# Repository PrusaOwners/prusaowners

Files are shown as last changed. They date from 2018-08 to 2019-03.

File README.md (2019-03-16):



# PrusaOwners

This is a wiki for the Original Prusa printers created by Josef Prusa and any projects related to these printers.

## Printer Information

### Prusa i3 Official Links
- [MK3 Features](https://www.prusa3d.com/original-prusa-i3-mk3/)
- [MK2s Features](https://www.prusa3d.com/prusa-i3-kit)
- [Printing Handbook](https://www.prusa3d.com/downloads/manual/prusa3d_manual_175_en.pdf)
- [Manuals and Guides](https://manual.prusa3d.com/c/English_manuals)
- [Drivers and downloads](https://www.prusa3d.com/drivers/)
- [Maintenance Guides](https://help.prusa3d.com/l/en/category/A6PvLnaCoU-maintenance)
- [Knowledge Base](https://help.prusa3d.com/l/en)
- [Store](https://shop.prusa3d.com/en/)

### Communities
- [Prusaowners Discord Server (The 602 Wasteland)](https://discord.gg/hYUjSnW)
- [Official Prusa Forums](https://shop.prusa3d.com/forum)
- [Original Josef Prusa i3/MK2/S/3 Owners](https://www.facebook.com/groups/Prusai3users/)
- [Prusa Community Forum and Custom Mods](https://www.facebook.com/groups/prusacommunity/)
- [Prusa I3 MK2/S/3 - FR (french)](https://www.facebook.com/groups/prusai3mk2s/)
- [Haribo 3030 Upgrade](https://github.com/PrusaMK2Users/3030_Haribo_Edition/)
- [Prusa i3 Bear Upgrade](https://www.facebook.com/groups/prusabearupgrade/)
- [3d Printing Matttermost Server](https://3dprinting.community)
- [r/prusa3d subreddit](https://www.reddit.com/r/prusa3d/)
- [r/prusa3d Discord](https://discord.gg/z7wMpfn)

## Resources

### Printer Specifications and Parts
- [MK3 Compatible Parts](MK3_Compatible_Parts.md)
- [EinsyRambo Specifications](https://reprap.org/wiki/EinsyRambo)
- [TMC2130 Stepper Driver Datasheet](https://www.trinamic.com/fileadmin/assets/Products/ICs_Documents/TMC2130_datasheet.pdf)

### Firmware
- [Klipper](Klipper.md)
- [Klipper MK3 Firmware G-Code Reference](https://github.com/KevinOConnor/klipper/blob/master/docs/G-Codes.md)
- [Prusa Official Firmware](https://github.com/prusa3d/Prusa-Firmware)
- [Prusa Official MK3 Firmware G-Code Reference](https://github.com/prusa3d/Prusa-Firmware/blob/MK3/Firmware/Marlin_main.cpp#L152)

### Slicing Software
- [Slicer Profiles](Slicer_Profiles.md)
- [Test Prints](Test_Prints.md)

### PrusaOwners Repositories
- [Main Github](https://github.com/PrusaOwners/prusaowners/)

### Community To Do List
- [Community To Do List for i3 MK3](Community_To_Do_List_for_i3_MK3.md)

## How To Guides

### How To Guides
- [Cold Pull on MK3](Cold_Pull_on_MK3.md)
- [gregsaun's maker cheatsheet](https://github.com/gregsaun/maker_cheatsheet)
- [Manual print based PINDA temperature calibration](Manual_print_based_PINDA_temperature_calibration.md)
- [First layer and PINDA temperature calibration with calipers](First_layer_and_PINDA_temperature_calibration_with_calipers.md)

### Mods and Improvements
- [Bed Leveling with Wave Springs](Bed_Leveling_with_Wave_Springs.md)
- [Bed Leveling without Wave Springs](Bed_Leveling_without_Wave_Springs.md)
- [Improved Rigid Feet](https://www.thingiverse.com/thing:2802540)
- [Improved Z-axis mounts by jltx](Improved_Z-axis_mounts_by_jltx.md)
- [Metal MK3 parts](Metal_Mk3_parts.md)
- [S3l3ctor](S3l3ctor.md)
- [Reverse Bowden](https://www.thingiverse.com/thing:2783385)
- [Skelestruder by jltx](Skelestruder_by_jltx.md)
- [How to make prints better on the mk3](How_to_make_prints_better_on_the_mk3.md)
- [PLA bearings](PLA_bearings.md)
- [Einsy fan voltage mod](Einsy_fan_voltage_mod.md)
- [Moons stepper motors](Moons_stepper_motors.md)
- [MK2 PINDA temp retrofit](https://github.com/PrusaOwners/prusaowners/blob/master/MK2%20PINDA%20temperature%20compensation%20retrofit.md)
- [Bear upgrade frame](https://github.com/gregsaun/prusa_i3_bear_upgrade)
- [Bear upgrade extruder and X axis](https://github.com/gregsaun/bear_extruder_and_x_axis)

### Octoprint
- [Prusa Guide: Octoprint for i3 MK3 using Pi Zero W to Einsy Headers](https://manual.prusa3d.com/c/Octoprint_for_Original_Prusa_i3_MK3)
- [PrusaMeshMap Plugin for Octoprint](https://github.com/PrusaOwners/OctoPrint-PrusaMeshMap)

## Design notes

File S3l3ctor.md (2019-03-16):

[This is S3l3ctor](https://github.com/PrusaOwners/s3l3ctor/blob/master/images/s3l3ctor.png), an open source, sub $100, 6 chroma filament selector system currently under development. You can print any color (up to 6) you want without changing your extruder design.

S3l3ctor is:
* A 100% open source filament selector
* Costs under $120
* Can use up to 6 colors at once
* Lets you keep your extruder
* Can work on any printer with a USB port or spare pins
* Being developed by Matt when he's not doing homework
* Is undergoing closed Alpha testing right now

S3l3ctor is **not**:
* Done yet
* Accepting donations not made in 4043d
* A MMU2 clone
* Requires changing extruder hardware
* For the faint of heart (yet!)

S3l3ctor is an open source filament selector under development. Development is being led by ThatMattGuy (Matt) in collaboration with other community members.

At this point the project is undergoing closed alpha testing and will have an open beta starting soon<sup>TM</sup>. I mean you print the parts, but it's likely not a good idea yet.

[Link the the Github STLs](https://github.com/PrusaOwners/s3l3ctor).

# BOM

## Printed Parts:

| STL Name | Quantity |
| ---- | ---- |
| MainBodyV2 | 1 |
| barrelidlerholder_v2.STL | 1 |
| barrelMotorholder_v2 .STL | 1|
| A1R1__Body_spring_x2.STL | 0|
| A1R1_AssemblyHolder_x2.STL | 2 |
| RetainerV2.STL | 2 |
| A1R1_SplitterShroom_x1.stl | 1 |
| A1R1_tumblerV64_maleEnd_x1.stl | 1 |
| A1R1_tumblerV64_motorEnd_x1.stl | 1 |
| A1R1_tumblerV69_pin_x6.stl | 6 |
| A1R1_tumblerV69_withsupports__x6.stl | 6 |
| For Skelestruder People: | |
| PC4-m10_SKELESTRUDER_B1.stl | 1|

## Hardware:

| Item | Quantity | Example link | 
|---- | ---- | ----|
| Bolts | (how many? What size?) | Soon^tm |
| Square nuts | 2 | Spares bag| 
| 608 bearings | 8 | [ebay](<https://www.ebay.com/itm/8pcs-625-2Z-625-ZZ-C3-Double-Metal-Shielded-Ball-Bearing-5x16x-5mm-US-Stock-M496/401542781331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>)  |
|Mk8 Gears| 6 | [Amazon](<https://www.amazon.com/BALITENSEN-Direct-Extruder-Reprap-Effective/dp/B07792SHML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>) |
|Pc4-M10 fittings, pass through or drill them out | 7| soon^tm|
|PTFE tubing ID 2mm OD 4mm | couple meters | [ebay](<https://www.ebay.com/itm/PTFE-Bowden-Teflon-Tube-1-75-Filament-3D-printer-RepRap-Rostock-Kossel/162932641530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>) |

## Electronics:

| Item | Quantity | Notes and URL|
|----|----|----|
|RAMPS + 5x A4988 drivers + Mega kit | 1 | [ebay link](https://www.ebay.com/itm/3D-Printer-Kit-RAMPS-1-4-Mega2560-A4988-12864-LCD-Controller-for-Arduino-Reprap-/252181241032) - TODO find a better kit link |
|**POWER OPTIONS**|||
|12v 2 amp power brick| 1| If you want to externally power S3l3ctor - [Example brick](https://www.amazon.com/Amamax%C2%AE-Wall-Adapter-Power-Supply/dp/B00KZ2ZQE8) - TODO find a better example
|12v 2 amp buck converter| 1| OPTIONAL - For those who want to run off a 24v PSU. Make sure you have enough PSU headroom! [Example](https://www.amazon.com/Converter-Step-Down-Module-Voltage-DCCON-CPT245/dp/B00BNPYBM4) - TODO verify links
| If you have a 12v PSU and want to power off the PSU| |You're fine, nothing needed here :D |
||||
| Microswitch with bearings | 9| [Something like this](https://www.google.com/url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)

For a RAMPS setup: Set of RAMPS plus at least 2x A4988s (usually 5x) plus Mega Either a 12v brick (2 or more amps) or 24v to 12v buck regulator off of printer PSU 2x NEMA 17s 7-8x microswitches with bearings

# Assembly

## Tumbler

### Shaft preperation

Begin by filing, grinding or otherwise abrating a flat a mm or two deep (doesn't really matter), and about 5mm long. While you have the shaft out, make sure that your 625 bearings will slide smoothly along the shaft. They shouldn't slide smoothly like a linear bearing, but at the same time they should not need pounding. A more scientific way to quantify this is with a calipers - if the bearings' ID is more than 30 micron undersized (4.97mm or so), the fit on the 5mm rod is going to be close. Like, probubly too close. I reccomend measuring bearings and 

## Main Body

## Magic Mushroom

## Electronics

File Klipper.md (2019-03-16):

About Klipper
-------------

Klipper is a 3D printer firmware system which utilizes an external processor such as a Raspberry Pi or other computer to compute kinematic equations and send the processed information to the MCU on the printer, usually a ATMega 2560. Klipper's main fork is available at <https://github.com/KevinOConnor/klipper>, however, if you want the experimental features outlined in this wiki it is recommended to clone our community repository at <https://github.com/PrusaOwners/klipper>.

Installing and Configuring Klipper on the MK3
---------------------------------------------

If you are installing Klipper on a Raspberry Pi, follow the instructions [Adafruit's put together here](https://learn.adafruit.com/octoprint-on-m3d/octoprint-set-up) to install Octoprint, or use a preconfigured octopi image.

First, SSH into the Pi (Windows: use PuTTY; Linux/Mac, use the terminal). If you don’t know what it is, try octopi.local or install something like Advanced IP Scanner to find it out. Username is pi, password raspberry

Run the following commands:

    git clone https://github.com/PrusaOwners/klipper
    ./klipper/scripts/install-octopi.sh
    cd ~/klipper/
    make menuconfig

Leave everything as stock, and click save, then exit.

Run the following command:

    make

Ensure that the Raspberry Pi is physically connected to the printer, and that Octoprint is not connected to the printer by navigating to <http://octopi.local> or your pi’s IP address on a web browser (the "Connect" button should be displayed).

Next is finding the USB serial port.  The general way to find a USB serial port is to run ls -l /dev/serial/by-id/ from an ssh terminal on the host machine. It will likely produce output similar to the following:

    lrwxrwxrwx 1 root root 13 Jun  1 21:12 usb-1a86_USB2.0-Serial-if00-port0 -> ../../ttyUSB0
The name found in the above command (minus the -> ../../ttyACM0 portion) is stable and it should be used in the config file and while flashing the micro-controller code. For example, a flash command might look similar to:

    sudo service klipper stop
    make flash FLASH_DEVICE=/dev/serial/by-id/usb-1a86_USB2.0-Serial-if00-port0
    sudo service klipper start

Next, copy the file ~/klipper/config/printer-prusa-i3-mk3-2017.cfg to your home directory and rename it printer.cfg:

    cd ~
    cp ~/klipper/config/printer-prusa-i3-mk3-2017.cfg printer.cfg

This file contains a default configuration for the Prusa i3 MK3 and enables all of the experimental features outlined in this wiki.  The config must be updated with the updated USB information.  Open up printer.cfg in a text editor and change the line listed below:

    [mcu]
    serial: /dev/ttyACM0

to match the the USB device from the ls -l command.  Be sure to copy-and-paste the name from the "ls" command (minus the -> ../../ttyACM0 portion) that you ran above as the name will be different for each printer.  The line in the updated config might look like:

    [mcu]
    serial: /dev/serial/by-id/usb-1a86_USB2.0-Serial-if00-port0

Next, restart Klipper with the following command:

    sudo service klipper restart

Finally, connect Klipper to Octoprint:

Go to the setting wrench at the top.

Under **“Serial Connection”** in **“Additional serial ports”** add **“/tmp/printer”**. Then click **“Save”**.

Enter the Settings tab again and under **“Serial Connection”** change the **“Serial Port”** setting to **“/tmp/printer”**. Navigate to the **“Behavior”** sub-tab and select the **“Cancel any ongoing prints but stay connected to the printer”** option. Click **“Save”**.

From the main page, under the **“Connection”** section (at the top left of the page) make sure the **“Serial Port”** is set to **“/tmp/printer”** and baudrate is **250000** and click **“Connect”**. (If **“/tmp/printer”** is not an available selection then try reloading the page.)

Once connected, navigate to the **“Terminal”** tab and type **“status”** (without the quotes) into the command entry box and click **“Send”**. If you see this, you’re good: **“Recv: // Printer is ready”**

Special considerations for installing on a non-raspberry-pi
-----------------------------------------------------------

If you follow the above instructions and it doesn't work, try running this:

cat /etc/default/klipper

You should get an output like this:

    # Configuration for /etc/init.d/klipper

    KLIPPY_USER=server

    KLIPPY_EXEC=/home/server/klippy-env/bin/python

    KLIPPY_ARGS="/home/server/OctoPrint/klipper/klippy/klippy.py /home/server/printer.cfg -l /tmp/klippy.log"

If KLIPPY_ARGS's path is different than your klipper path (e.g. this example shows Klipper under the Octoprint folder, and I had it in /home/server), correct with a mv command like so: mv /home/YourUserName/klipper /home/YourUserName/OctoPrint/klipper

Calibrating your Z-Endstop
--------------------------

The Prusa i3 MK3 uses the Pinda probe as a Z-Endstop, and the endstop height needs to be calibrated prior to printing. Proceed with the following steps for initial calibration:

1.  Set the following properties under [stepper_z] in your printer.cfg:

        position_min: -2
    and under [probe]:

        z_offset: 0

2.  Restart klipper from the shell to load the new config:

        sudo service klipper restart

    Alternatively, you can issue a restart command from Octoprint's terminal if you are connected.

3.  Home the Z-axis using Octoprint.
4.  Use Octoprint or the Printer Menu to move the Z-axis down in .1mm to .01mm increments until the nozzle is just above the bed
5.  The current Z position will likely be somewhere between -0.4 and -1.0 It will be displayed on the printer, you can also retrieve the current position by issuing the GET_POSITION command in Octoprint's terminal.
6.  The absolute value of the current Z position will be your endstop position and probe offset. For example, if your Z position is -.6, enter the following under [probe]:

        z_offset: .6

7.  Restart Klipper again and you are ready to print. You may have to make slight changes to get a good first layer. Increasing the endstop position will bring the nozzle closer to the bed when printing, decreasing the endstop will raise it. Make sure you update both the endstop position and probe offset when making changes.

Prusa GCode Support
--------------------

Currently the following prusa specific gcodes are supported:

-   TIMED_GCODE
-   TRAM_Z

To enable these gcodes, add the following to your printer.cfg:

    [prusa_gcodes]

TIMED_GCODE allows the user to execute a gcode with a specific delay.  This is, for example, useful for resetting the display after a M117 message.  It is used in the following manner:

    TIMED_GCODE GCODE=M117 DELAY=5

The example above will send an empty M117 with a delay of 5 seconds.  Note that if you want to execute a more complex gcode, spaces should be replaced underscores.  For example, if you want to send M117 Hello on a with a delay of 10 seconds, you could enter the following:

     TIMED_GCODE GCODE=M117_Hello DELAY=5

TRAM_Z functions in a manner similar to Prusa's Calibrate-Z functionality. It will use the TMC2130 driver to home to the top of the printer, then move an extra 10mm to “tram” the Z-Axis.

Note for previous users:
LOAD_FILAMENT, UNLOAD_FILAMENT, SET_BEEPER, and M900 have been deprecated.  It is recommend to use gcode macros to replace the functionality of these gcodes.

Configuring Mesh Bed Leveling
-----------------------------

### About Klipper Mesh Bed Leveling

Mesh Bed Leveling is now available in upstream Klipper: <https://github.com/KevinOConnor/klipper>

You may also pull it from the PrusaOwners repo: <https://github.com/PrusaOwners/klipper/>

### Things to Note Before Implementing

There are a few things to keep in mind with this implementation that may be subject to change:

1.  By default each probe point is only sampled once, unlike Prusa Firmware which samples twice. After testing this doesn't seem to create an issue, as the Pinda produces fairly repeatable results. Functionality has been added to multi-sample points, with the tradeoff being that there is a small pause between samples unlike stock firmware.
2.  <b>Those transitioning from ALPHA versions of bed_mesh should be aware of the following:</b>
    1.  The probe_offset option of [bed_mesh] has now moved to the [probe] section as x_offset and y_offset.
    2.  In the [bed_mesh] section probe_min and probe_max have been renamed to min_point and max_point.
    3.  G80 and G81 aliases are no longer hardcoded. Instructions for how to add aliases via gcode_macros are provided later in this document.
    4.  After probing the tool no longer returns to (0,0), as this is not suitable for every printer. This can be added in a gcode_macro or in your slicer's start gcode.

### Pre-requisites

Before proceeding, make sure [bed_tilt] is not in your printer.cfg. It will present a conflict with Mesh Leveling. You also need [probe] in your printer.cfg:

    [probe]
    pin: PB4
    x_offset: 24.
    y_offset: 5.
    z_offset: .0
    speed: 10.0

The z_offset is the distance between the nozzle and the print surface when the probe triggers.  When a probe is used as an endstop for the z axis, the value for z_offset will be used as the endstop position.  Thus, if you have position_endstop in [stepper_z] defined, remove it.  The x_offset and y_offset options refer to the distance between the nozzle and the probe on their respective axis.

It is also a good idea to make sure position_min under [stepper_z] is a negative number. Its likely that you will need to move below Z0 if your bed is significantly warped.

Finally, I recommend adding a homing override to to home to the center of the bed:

    [homing_override]
    gcode:
     G1 Z3
     G28 X0 Y0
     G1 X101 Y100 F5000
     G28 Z0
    set_position_z: 0

This will lift Z 3mm prior to homing, making sure that it doesn't crash into the bed if its location is close to the build plate. It will then home X and Y, move X and Y so that the probe is at the center of the build plate, then home Z.

### Configuration

Mesh Leveling is fully parametric. As a result it is possible to configure it for any printer, and a varying number of probe points. Probe points are generated dynamically. To get started with Mesh Leveling, the bare minimum is required in printer.cfg:

    [bed_mesh]
    speed: 100
    min_point: 11,1
    max_point: 215,193

Below is what a Mesh Bed Leveling configuration would look like with all options set:

    [bed_mesh]
    speed: 100
    horizontal_move_z: 5
    samples: 1
    sample_retract_dist: 2.0
    min_point: 11,1
    max_point: 215,193
    probe_count: 3,3
    fade_start: 1.0
    fade_end: 10.0
    move_check_distance: 5.0
    split_delta_z: .025
    mesh_pps: 2,2
    algorithm: lagrange
    bicubic_tension: .2

Be aware that when dynamically generating points the distance between each point is calculated. If the distance is not a whole number, the value will be floored to the last hundredth. This will result in your maximum points being adjusted inward slightly. Also keep in mind that the min and max points refer to the position of the nozzle, not the probe. Make sure you do not choose points that will move the probe off of the bed.

Below is a detailed explanation of each option:

-   speed:

The speed at which the bed is probed.

-   horizontal_move_z:

The distance to raise the toolhead between probes. Default is 5mm.

-   samples:

The number of samples to take for each probe point.

-   sample_retract_dist:

The distance to retract the tool between samples.  Only applies when samples > 1.

-   min_point:

The minimum start point (x,y) on the grid to generate. This parameter must be provided.

-   max_point:

The maximum start point (x,y) on the grid to generate. Note that this may not be the 'last' point if probing an even number of Y values on the grid. This parameter must be provided.

-   probe_count:

A comma separated pair of integers (x,y) indicating the number of points to probe on each axis. It is possible to enter a single integer value for this parameter, in which case it will be applied to both axes. Default is 3,3.

-   fade_start:

The z position in which to start fading out z_adjustment. Default is 1.0

-   fade_end:

The z position in which fading will complete. If fade_end is less than or equal to fade_start then fading will be disabled. Be careful with this setting, fading too quickly will likely result in a failed print, or could potentially crash the nozzle into the bed if done near Z0. Default is 10.0

-   move_check_distance:

The minimum distance a move can be split. Default is 5.0

-   split_delta_z:

The minimum amount of z-difference that will trigger a split move. The check algorithm will traverse a move by the amount specified in move_check_distance until it finds a z-delta greater than or equal to split_delta_z. Default is 0.025

-   mesh_pps:

A comma separated pair of integers (x,y) indicating the number of points to interpolate for each segment in the axis. Consider a 3x3 probed grid. There are two “segments” between the X points, and two between the Y points. If you specify mesh_pps: 3,3 then there will be 6 interpolated points and 3 probe points in the mesh along each axis, for a total of 81 points in the mesh. If this is set to zero, then no interpolation will be done on the axis. Note that this value can also be a single integer, in which case the number is applied to both axes. Default is 2,2.

-   algorithm:

The interpolation algorithm to use. May be either “lagrange” or “bicubic”. 3x3, 4x3, and 3x4 meshes must use lagrange, 4x4 or above may choose either. Default is lagrange.

-   bicubic_tension:

The bicubic interpolation algorithm uses cardinal hermite spline interpolation. A “tension” parameter may be entered to influence the amount of slope interpolated in the curve. That is, a higher tension will will make the mesh more curvy, and zero tension will be closer to bilinear interpolation. Be careful with this setting as generating steep hills and valleys in the mesh may cause the the nozzle to crash. This setting will be ignored if not using bicubic interpolation. Default is 0.2.

### Bed Mesh Gcodes

    BED_MESH_CALIBRATE

Initiates the calibration procedure (ie probes the bed and builds the mesh).

    BED_MESH_OUTPUT

Prints the results of the Mesh to the terminal.

    BED_MESH_MAP

This will probe the bed, serialize the points, and send them to the terminal. No mesh will be generated during this procedure, so no correction will be applied. It will however clear any prior mesh data. The purpose of this gcode is to allow for Octoprint plugins such as PrusaMeshMap to easily fetch probe data from a large number of sampled points. This has not yet been implemented in any plugins, but the functionality is there for those who wish to take advantage of it.

    BED_MESH_CLEAR

This will clear the mesh from memory. No further Z adjustment will be performed after a clear.

    BED_MESH_PROFILE LOAD=<name> SAVE=<name> REMOVE=<name>

BED_MESH_PROFILE can be used to save mesh state to persistent storage.  This isn't advised for MK3 users as bed geometry may not be consistent between prints, However users with rigid beds and glass surfaces may find this functionality useful.

### Generating Aliases

To generate gcode aliases, the following can be added to your printer.cfg:

    [gcode_macro G80]
    gcode:
     G28
     BED_MESH_CALIBRATE
     G1 X0 Y0 Z0.4 F4000

    [gcode_macro G81]
    gcode:
     BED_MESH_OUTPUT

This will create G80 and G81 aliases respectively. Also, as you can see, the G80 Macro moves the tool back to the origin after calibration. You can alter this GCode line to move it where you please at a speed that best suits your printer.

### Final Notes

-   Generally probing a 3x3 grid with default mesh values will produce the desired result. However, one may wish to experiment with more probe points and different interpolation algorithms to eliminate deadspots. Lagrange interpolation tends to oscillate as the number of samples increase, so it is recommended to use bicubic interpolation for larger probe grids.

Bed Skew Correction:
--------------------
TODO (COMING SOON)

Pressure Advance
----------------

The next thing you'll have to do is to configure _Pressure Advance_ (from this point downwards _PA_). Without _PA_ you will be getting ugly prints with blobs and curling at corners and lots of oozing. There is a [guide](https://github.com/KevinOConnor/klipper/blob/master/docs/Pressure_Advance.md) on how to configure _PA_ in the main Klipper repository, but it is complex and requires lots of manual steps. Read it through to understand what it is about, but don't actually follow it. We provide a setup process which is mode advanced and simpler at the same time, where you only have to print one test object from which you can derive the _PA_ value. The guide is [here](Pressure_Advance.md).

[Alpha] Probe Temperature Compensation
----------------------------------------

Initial support has been added for probe temperature drift compensation. In its current form temperature compensation is configured manually, in a similar fashion to the method used in stock Prusa firmware.

To enabled Probe temperature support, add the following to your printer.cfg:

    [probe_temp]
    sensor_type: EPCOS 100K B57560G104F
    sensor_pin: PF3
    t_offsets:
     35.0, 0.0
     40.0, 0.02
     45.0, 0.06
     50.0, 0.120
     55.0, 0.2
     60.0, 0.3

Note that the offsets above are Prusa Firmware's defaults. Also note the space padding the front of each offset. This is <b>required</b>, otherwise Klipper's parser will get confused.

The following gcodes are added with this module:

    GET_PROBE_TEMP

This simply returns the probe's current temperature to octoprints terminal

    PROBE_WAIT TEMP=<Target Temperature> TIMEOUT=<SECONDS>

Use the gcode above to wait for the probe to reach a certain temperature. The minimum target is 20, maximum is 70. The direction is automatically determined by the heater state.  If both heaters are off then the gcode will wait for the probe to cool to the supplied temperture, otherwise it will wait for it to heat.  Timeout sets a timeout in minutes. If the timeout is reached the printer will stop waiting and no changes will be made to the offset. A timeout value of 0 will wait indefinitely, which is the default value. 

    APPLY_TEMP_OFFSET

The gcode above will look up the probe's current temperatue, calculate the offset to apply based on the supplied parameters, then adjust the gcode offset by that amount.

### Manual Calibration Procedure

1.  Before Calibrating, make sure to remove t_offsets and all of its associated values from printer.cfg, then restart Klipper. This will make sure that no additional offset is applied during calibration.
2.  Use a gcode similar to what is used for manual probe calibration on Prusa Firmware. A single layered object with a large surface area works well.
3.  Your start gcode should look something like the following:
        M83  ; extruder relative mode
        M104 S210 ; Set nozzle temp
        M140 S60 ; set bed temp
        M190 S60 ; wait for bed temp
        M109 S210 ; wait for extruder temp
        G28 ; home axes
        G1 X50 Y50 Z.4 ; move printhead to a good warming position
        PROBE_WAIT TEMP=40 DIRECTION=heat ; wait for the probe to reach 40C
        G80 ; mesh leveling
        G1 X0 Y-3.0 F3000.0 ; go outside print area
        G92 E0.0
        G1 X60.0 E9.0  F1000.0 ; intro line
        G1 X100.0 E12.5  F1000.0 ; intro line
        G92 E0.0

    Adjust the above to your filament requirements. You may be able to move your nozzle closer to the bed when warming, but be careful as mesh leveling has not yet been applied to compensate for warped bed geometry. Also note that bed geometry changes as heat is applied.

4.  Use Klipper's SET_GCODE_OFFSET Z_ADJUST=[value] to act in a similar manner to live-z. Note that positive and negative offsets can be mapped to buttons (see Octoprint's Custom Control Editor plugin). A z_adjust value of +/-.02 is a good place to start, continue adjusting until you have your desired first layer
5.  Use GET_POSITION to get your total z_offset. Your output will look something like this:
        Send: GET_POSITION
        Recv: // mcu: x:-4778 y:-5497 z:-25
        Recv: // stepper: x:50.000000 y:50.000000 z:50.000000
        Recv: // kinematic: X:50.000000 Y:50.000000 Z:50.000000
        Recv: // toolhead: X:50.000000 Y:50.000000 Z:50.000000 E:0.000000
        Recv: // gcode: X:50.000000 Y:50.000000 Z:49.980000 E:0.000000
        Recv: // gcode base: X:0.000000 Y:0.000000 Z:-0.020000 E:0.000000
        Recv: // gcode homing: X:0.000000 Y:0.000000 Z:-0.020000

    The Z value next to gcode base is your total z adjustment. In this example, drift at 40C increased by .02, as an offset of -.02 was added to compensate. The value 40.0, 0.02 should be added to t_offsets in printer.cfg. NOTE: If you are already using SET_GCODE_OFFSET to adjust your nozzle height, don't forget to account for it.

### Auto Calibration Testing

Currently there is no automatic calibration because we simply do not have enough data, and the data we have is wildly consistent. For example, in our experiments, drift at X50 Y50 with only the bed on results in insignificant drift. With the extruder on, at the same position, drift increases significantly. The amount of drift increases with higher extruder and bed temperatures.

However, if the probe is repositioned directly over the center standoff on the bed, roughly X97 Y103, the probe actually triggers LOWER. This holds true at high extruder and bed temperatures. This phenomenon suggests that “drift” may not be related to the Probe, but rather to a change in bed geometry. If that is the case then drift can simply be overcome with a more accurate mesh when applying leveling.

That being said, more data will lead to a more solid conclusion, and if the probe itself is indeed experiencing drift, then perhaps we can come up with a way to automatically compensate for it. If you are interested in collecting this data, read on.

The current probe_temp implementation includes the following gcode:

    CALIBRATE_PROBE_TEMP X=97 Y=103 TARGET=45 B_TMP=70 E_TMP=200 TIMEOUT=180

Currently the gcode doesn't actually calibrate the sensor. It gathers temperature and drift data, serializes it, and dumps it to a file. As you can see there are several options, which are explained below. The values for each option above are defaults, any option may be left out if you desire a default value.

-   X - X position from which to gather probe data
-   Y - Y position from which to gather probe data
-   TARGET - The target temperature for the Pinda to reach. Once it has been obtained collection will end.
-   B_TMP - The bed temperature to set
-   E_TMP - The extruder temperature to set
-   TIMEOUT - The maximum time, in seconds, between each sample. If timeout is reached collection will end.

When calibration is complete (or times out) data will be dumped to ~/PindaTemps.json. It is useful to calibrate at the default position (center standoff) and one other position such as X50 Y50, up to a target temp of 55 to 60C. To reach these probe temperatures it is recommended to heat the extruder to a minimum 235C and the Bed to 90C.

If you are interested in collecting data, please visit the \#mk3-klipper channel on the Prusa3d-Users discord server.

Filament Sensors
----------------

The MK3 and MK3S both have a filament sensor, but they each use a different type of sensor. In order to use them with Klipper you'll need to update your printer.cfg with the appropriate section below, then add/update the common sections to your printer.cfg. Look in the example-extra.cfg for more details. You must use Klipper's RESUME command and not OctoPrint's once a runout has been detected and filament has loaded. 

### MK3 Filament Sensor (pat9125)

    [pat9125 fsensor]
    pause_on_runout: True
    runout_gcode:
        M118 Filament Runout Detected
        M600 X250 Y-3 Z10
    insert_gcode:
        M118 Filament Load Detected
        LOAD_FILAMENT
    invert_axis: True
    oq_enable: True

### MK3S Filament Sensor

    [filament_switch_sensor fsensor]
    pause_on_runout: True
    runout_gcode:
        M118 Filament Runout Detected
        M600 X250 Y-3 Z10
    insert_gcode:
        M118 Filament Load Detected
        LOAD_FILAMENT
    event_delay: 3.0
    switch_pin: !PK0

### Common configuration for both

You will need to add the following sections to you printer.cfg so that the M600 and LOAD_FILAMENT commands in the above work as intended. You can adjust the gcodes to suite your need, as long as the M600 starts with Klipper's PAUSE command.

    [respond]
    default_type: command

    [pause_resume]

    # Filament change gcode, parameters are a default park position if no XYZ is specified  - Z is relative.
    [gcode_macro M600]
    default_parameter_X: 100
    default_parameter_Y: 0
    default_parameter_Z: 10
    gcode:
        PAUSE
        G91
        G1 E-.8 F2700
        G1 Z{Z}
        G90
        G1 X{X} Y{Y} F3000
        M117 Ready for unload

    [gcode_macro LOAD_FILAMENT]
    gcode:
        M117 Loading Filament...
        G1 E70 F400
        G1 E40 F100
        G92 E0.0
        M400
        M117 Load Complete

    [gcode_macro UNLOAD_FILAMENT]
    gcode:
        M117 Unloading Filament...
        G1 E0.5 F1000
        G1 E-0.5 F1000
        G1 E1.0 F1000
        G1 E-1.0 F1000
        G1 E1.5 F1000
        G1 E-1.5 F1000
        G1 E2.0 F1000
        G1 E-100 F3000
        M400
        M117 Remove Filament Now!
        M300 S300 P1000

These two are not strictly needed, but they are useful to add - They add a __Change Filament__ and __Resume__ to the Filament menu on the display.
````
[menu __filament __change]
type: command
name: Change Filament
gcode:
    M600

[menu __filament __resume]
type: command
name: Resume
gcode:
    RESUME
````

### Notes

You can check the status of the filament sensor with the following command
    QUERY_FILAMENT_SENSOR SENSOR=fsensor
If you are using the 'filament_switch_sensor' and the status is inverted, then you just remove the ! on the 'switch_pin' so that it reads
    switch_pin: PK0
If you are using an older version of OctoPrint (<0.16) then you will also need to edit OctoPrint's config.yaml and add `unknownCommandsNeedAck: true` to the serial section. It should look something like this.
````
serial:
    additionalPorts:
    - /tmp/printer
    baudrate: 250000
    unknownCommandsNeedAck: true
    disconnectOnErrors: false
    logPositionOnCancel: true
    port: /tmp/printer
````
You need to SSH into your Pi or use SFTP. The file should be in ~/.octoprint directory.

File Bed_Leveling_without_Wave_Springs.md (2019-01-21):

# Bed Leveling without Wave Springs

> If your heated bed only has 6 screws holding it to the y-axis, this approach will not work. This is the case with Mk2.5 -> Mk3 upgrade kits.

Having levelled my bed with wave springs (using the more common single wave springs) I got great results initially, but over time I had to keep adjusting due to thermal variation and so on, but to compensate for this I had to keep adjusting the screws downwards as the wave springs gradually lost their spring. After a couple of months I ended up with flat washers instead of wave springs, and thus decided to try this approach.

The idea is to take out the reliance on a compressed spring, which will gradually lose it's un-sprung shape and tension, and instead make it a threaded adjustment. Basically instead of relying on a spring to push the bed up to the top of each screw, make it so the bed and screw are held together more tightly in the first place, and just use the thread to adjust the height more directly

The other benefit of this approach, is having a single fixed reference point. One of the downsides of using spring washers on all 9 bed points is never knowing which point to adjust.

By making the center point an absolute fixed reference, and adjusting other points around it, it actually makes the leveling process far easier and more intuitive.

Unfortunately the standard Mesh bed leveling output is not relative to any single fixed point, adding to the usual confusion about what's actually changing. i.e. if you change one point on the bed the numbers for all points change, regardless of whether they actually move or not. By making a simple firmware change to make the mesh-leveling output have all points relative to the center (without actually affecting the leveling algorithm) bed leveling is far more intuitive. (This could also be accomplished by changing the plugin, which I will investigate, but I like to be able to use the numbers without the plugin, for more absolute values ... you can use the actual mm offset to determine how far to turn each screw, remembering that one full turn is 0.5mm)

## Installation/Setup Procedure

Before starting you will need 8x M3 Nylock nuts (aka nylon lock nuts)

1. Move the Z axis to the top, to ensure it doesn't cause an obstruction
2. Ensure the heated bed and nozzle have cooled down
3. Turn off power to the printer
4. Remove the steel sheet from the heated bed
5. Remove all 9 screws from the heated bed, and set safely aside
6. Carefully lift the heated bed off the Y carriage, and rotate out of the way (optionally you may wish to disconnect the heated bed cables. It's probably safer to do this at the einsy end. Be particularly careful of the sensor cable)
7. Remove and store the metal spacers/standoffs
8. Put one of the M3 countersunk screws back into one of the holes in the perimeter of the heated bed
9. Optional: put a nylon M3 washer on the screw thread, on the underside of the bed. (I have not done this, so am not sure how this will affect leveling consistency, but it might make adjustment easier in theory)
10. Put one of the Nylock nuts onto the thread of the nut, on the underside of the bed, making sure of the orientation of the nut (the end with the white nylon visible goes away from the bed, most visible)
11. Tighten the Nylock nut and screw, using an allen-key/hex-wrench and a 5.5mm wrench or socket
12. Tighten until the nylock nut just starts to bite down against the bed, so the screw does not turn freely without the nut being held, then back the nut off a tiny amount (1/16th turn or less) so that the screw can be turned, but is not loose
13. Repeat steps 8-11 for each of the 8 perimeter holes
14. Place one of the spacers removed earlier over the center hole in the Y carriage
15. Place the remaining M3 screw through the center hole in the bed
16. Place the heatbed over the Y carriage, so that the center screw goes into the spacer, and is over the center hole.
17. Orientate the heatbed so that the screws (held in place by the lock nuts) are each aligned over their respective holes in the Y carriage
18. Starting with the front-center screw tighten it by one full turn (NOT more than one full turn)
19. Repeat for each of the perimeter screws in turn, I suggest following a clockwise pattern, turning each screw one full turn at a time.
20. Repeat the full circle 6-8 times, tightening each screw no more than one full turn at a time, and ensuring that each screw is tightened evenly on each rotation.
21. Check to see when the bed is sitting loosely on the center spacer (look underneath the bed, using a flashlight/torch if needed). Repeat tightening of each of the perimeter screws until the bed is sitting lightly on the center spacer.
22. Tighten the center screw. If the screw requires more than one full turn from when the screw starts to bite, for it to become tight, then you may need to further tighten the perimeter screws slightly
23. Check that a spacer can be fitted snugly between the bed and the Y-carriage near each of the perimeter screws. Adjust each screw as needed in order to be able to fit a spacer. Do not leave the spacer in place, just use it as a height gauge and then remove.
24. The bed should now be roughly level (probably VERY roughly, don't expect good numbers yet)
25. Reconnect the heatbed cables if they were disconnected previously.
26. Install the steel sheet on the heatbed
27. Turn on the printer, and run the first mesh bed leveling with the heatbed cold.

Hopefully this photo, showing the front-center screw, with the center spacer visible behind it, might help make this a little clearer: -

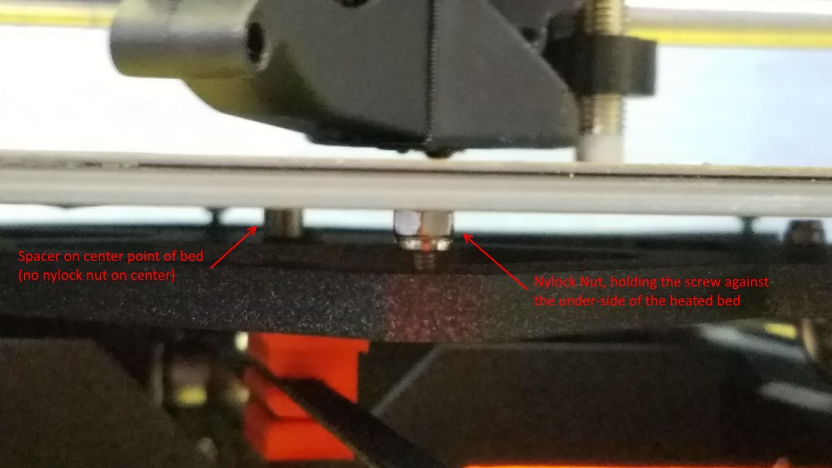
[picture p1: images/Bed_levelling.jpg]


## Leveling Procedure

After initial installation I would suggest first leveling with the bed at ambient temperature, since you should be able to get it fairly flat at ambient, and then only see minor variation when heated. You can then make fine adjustments at your usual bed temperature to get the best level possible.

I also strongly suggest using the firmware tweak below, in order to make the mesh-leveling command (`G81`) output have all points relative to the fixed center. This makes leveling much more intuitive. It's often easier to get a close level using the actual numbers, rather than the mesh-leveling plugin, since you can work out from the numbers roughly how far each screw needs to be rotated (there will be some variation partly due to slop between the screw thread and the thread in the Y carriage threads)

### Steps using terminal/numbers

1. Type `G80` into the terminal (whether using Octoprint, or a serial terminal with the einsy connected to PC)
2. Wait for the mesh leveling to complete
3. Type `G81` into the serial terminal

You should see output something like:

| | | | | | | |
|---|---|---|---|---|---|---|
| **-0.48750** | -0.42093 | -0.36621 | **-0.32334** | -0.29232 | -0.27315 | **-0.26584** |
| -0.21917 | -0.18561 | -0.16191 | -0.14806 | -0.14407 | -0.14993 | -0.16565 |
| -0.04861 | -0.03746 | -0.03468 | -0.04028 | -0.05425 | -0.07660 | -0.10732 |
| *' 0.02416*' | 0.02352  | 0.01546  | **0** | -0.02287 | -0.05315 | **-0.09084** |
| -0.00084 | -0.00268 | -0.01147 | -0.02723 | -0.04993 | -0.07959 | -0.11621 |
| -0.12361 | -0.11604 | -0.11549 | -0.12195 | -0.13543 | -0.15592 | -0.18343 |
| **-0.34417** | -0.31658 | -0.29658 | **-0.28417** | -0.27936 | -0.28213 | **-0.29250** |

Note this is using the firmware tweak below, making all numbers center-relative. If not using the firmware tweak, subtract the number of the center point from the others. You only care about the perimeter points that I've highlighted above

You can see from the numbers above that most of the points are lower than the center and, for example, the rear left point needs to be raised almost 0.5mm, or one full turn of the screw anti-clockwise. The rear right screw needs to be adjusted by a fraction over a half turn.

(remember that if not using the firmware tweak below, you'll need to subtract the value of the center point, in order to get the relative values) Ignore all the fictional numbers, especially since the algorithm used to derive them seems utterly broken (I think they're trying to do a curve fit, but with a poor choice of params, though I haven't actually spent the time to look at the algorithm in the firmware).

Adjust all 8 perimeter screws by roughly the amount indicated in the first pass. In subsequent passes focus on the 2 or 3 worst points each time, just to make it easier to make fine adjustments, and see the affect on the other 7 points (there will be some minor effect on adjacent or opposite points, just because the screws are not tight. (I have considered using a regular nut to lock the thread against the Y carriage, but this would be a lot more work, and seemed unecessary based on my testing thus far)

Repeat the calibration steps above, making finer and finer adjustments each time.

Once you're within say 0.05mm, you may wish to switch to doing the calibration with the bed at your normal printing temperature (e.g.: 60&deg;C)

Repeat until the level is within 0.05mm. You can probably get the level to around 0.02mm variation fairly easily, and with a little patience even closer (but don't get too obsessed,as you'll see little real benefit from your effort if trying to strive for perfection)

Hopefully you might be able to end up with numbers more like these (not actually the best number I got)

| | | | | | | |
|---|---|---|---|---|---|---|
| **-0.00667** | -0.00731 | -0.00704 | **-0.00583** | -0.00370 | -0.00065 | **0.00333** |
| -0.00565 | -0.00560 | -0.00461 | -0.00269 | 0.00017  | 0.00397  | 0.00570 |
| -0.00454 | -0.00430 | -0.00303 | -0.00074 | 0.00258  | 0.00593  | 0.00631 |
| **-0.00333** | -0.00343 | -0.00231 | **0** | 0.00352  | 0.00624  | **0.00817** |
| -0.00204 | -0.00297 | -0.00245 | -0.00046 | 0.00298  | 0.00789  | 0.00826 |
| -0.00065 | -0.00294 | -0.00344 | -0.00213 | 0.00098  | 0.00588  | 0.00659 |
| **0.00083** | -0.00333 | -0.00528 | **-0.00500** | -0.00250 | 0.00222  | **0.00617** |

### Using Octoprint Plugin

TBC

### Using g81_relative script

You can also use https://pcboy.github.io/g81_relative/ to convert the absolute values to relative ones. Simply paste the values you get from the g81 command in Octoprint in the first text area and you'll get relative values in the bottom text area.

## Firmware Tweak

In order to make the output be center-relative, without changing the actual compensation algorithm, I simply made the terminal output center-relative, without touching anything else.

In marlin_main.cpp search for `G81` and make the following additions:

```cpp
       /**
        * G81: Print mesh bed leveling status and bed profile if activated
        */
       case 81:
           if (mbl.active) {
               SERIAL_PROTOCOLPGM("Num X,Y: ");
               SERIAL_PROTOCOL(MESH_NUM_X_POINTS);
               SERIAL_PROTOCOLPGM(",");
               SERIAL_PROTOCOL(MESH_NUM_Y_POINTS);
               SERIAL_PROTOCOLPGM("\nZ search height: ");
               SERIAL_PROTOCOL(MESH_HOME_Z_SEARCH);
               SERIAL_PROTOCOLLNPGM("\nMeasured points:");
               
               float midPoint = mbl.z_values[((MESH_NUM_Y_POINTS+1)/2)-1][((MESH_NUM_Y_POINTS+1)/2)-1];
               for (int y = MESH_NUM_Y_POINTS-1; y >= 0; y--) {
                   for (int x = 0; x < MESH_NUM_X_POINTS; x++) {
                       SERIAL_PROTOCOLPGM("  ");
                       SERIAL_PROTOCOL_F(mbl.z_values[y][x] - midPoint, 5);
                   }
                   SERIAL_PROTOCOLPGM("\n");
               }
           }
           else
               SERIAL_PROTOCOLLNPGM("Mesh bed leveling not active.");
           break;
```

Compile the firmware changes, and flash to the Mk3. You should now always see the center point in the `G81` output be 0.0

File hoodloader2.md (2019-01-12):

Hoodloader2
================
Why Hoodloader2?
----------------
USB serial communication problems are common on the Einsy Rambo, affecting users both on stock Prusa Firmware using Octoprint and users that have migrated to Klipper. There are various factors involved with connection issues, however the most glaring culprit is the firmware running on the Atmega 32u2 processor that serves as a bridge for USB communication between the host machine (likely Raspberry Pi) and the Einsy's main processor, an Atmega 2560.

Hoodloader2 has functionality that goes beyond simple serial communications, however its primary benefit is vastly improved stability for USB and support for up to 2M baud full duplex serial communications.

Caveats
-------
* Because Hoodloader2 supports uploading sketches to the 32u2 in addition to the Atmega 2560, a baud rate of 57600 is reserved.  Thus you cannot connect to USB serial using this baud rate.  But really, why would you want to do that?

* Your Einsy will no longer enumerate using Prusa's Vendor and Product IDs.  It will show up as either "Hoodloader2 Mega" or as "Arduino Mega", depending on your platform.

* You will need a programmer to flash back to a standard DFU-usbserial setup.  However an Arudino can be flashed to work as a programmer without much of an issue.

Recommended - Record the serial number for your Prusa Einsy
-----------------------------------------------------------
Just in case you want to keep it.  With your MK3 powered on and connected to a Pi, ssh into the Pi and enter the following command:

```dmesg | grep usb```

Your output should look something like the below:

```script
[71569.010832] usb 1-1.4: new full-speed USB device number 10 using dwc_otg
[71569.155624] usb 1-1.4: New USB device found, idVendor=2c99, idProduct=0002
[71569.155639] usb 1-1.4: New USB device strings: Mfr=1, Product=2, SerialNumber=3
[71569.155648] usb 1-1.4: Product: Original Prusa i3 MK3
[71569.155657] usb 1-1.4: Manufacturer: Prusa Research (prusa3d.com)
[71569.155665] usb 1-1.4: SerialNumber: ALPHANUMERIC123
```
Record and save whatever is in the Serial Number Field.

Installing Hoodloader2
-----------------------
Hoodloader2 may be installed by using an Arduino Uno, or via progammer.  Both methods are covered in this document.

Install Method 1:  Arduino Uno
------------------------------
This method uses an installation sketch uploaded to an Arduino to flash the Einsy's Atmega 32u2.  While this document covers how to use an Arduino Uno, other Arduino's such as a Nano should work.  You will need 3 dupont male to female jumpers, and 3 dupont female to female jumpers.

1) Download the latest version of the Arduino IDE.
2) Clone the Hoodloader2 git repository:
`git clone https://github.com/NicoHood/HoodLoader2.git`
3) Open the sketch in the Hoodloader2 repo located at:
`/avr/examples/Installation_Sketch/Installation_Sketch.ino`
4) Change line 11 to the following:
`#define HEXFILE HEXFILE_HoodLoader2_0_5_Mega_atmega32u2_hex`
5) Save and upload the sketch to your Uno.
6) Disconnect your Einsy from USB and Power.  Disconnect your Uno from USB.
7) Use the following diagram to make your connections:
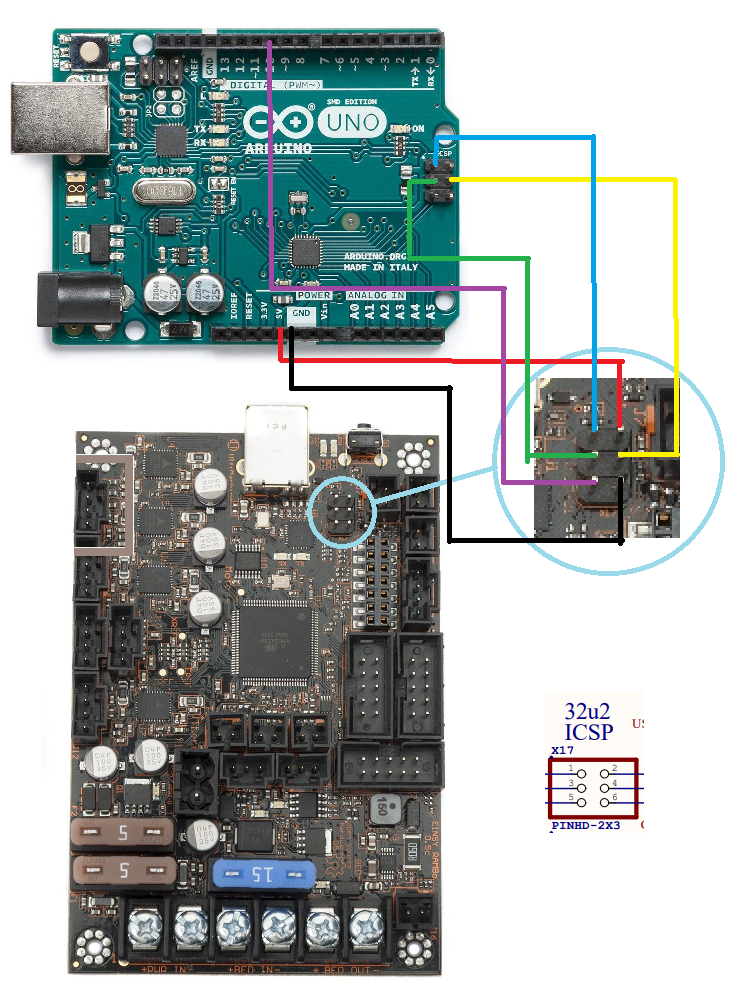
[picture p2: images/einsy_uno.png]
<File:einsy> uno.png


| Uno Pin | Einsy ICSP Pin | Color |
|---|---|---|
| MISO | Pin 1 (MISO) | Blue |
| +5v | Pin 2 (USBVCC) | Red |
| SCK | Pin 3(SCK) | Green |
| MOSI | Pin 4(MOSI) | Yellow |
| Pin 10  | Pin 5 (Reset)| Purple |
| Ground | Pin 6 (Ground) | Black |

8) Connect your secondary Arduino to your PC via USB.  Open the Arduino IDE's serial console at 115200 baud.  Watch as the firmware upload completes.
9) Disconnect everything.  Connect power and USB back to your Einsy.  Run the following command if connected to a linux based system such as a Raspberry Pi:
`ls /dev/serial/by-id/`
The output should be:
`usb-NicoHood_HoodLoader2_Mega-if00`
10) You are now ready to print with improved communication stability.

Install Method 2: Programmer
----------------------------------------
602 Wasteland community leader Zbrozek has contributed a simple method for programming with a USBasp.

1) Disconnect USB and Power from the Einsy
2) Connect the USBasp to the Einsy:

| USBasp | | Einsy ICSP|
|---|-|---|
| Pin 1 | MOSI | Pin 4 |
| Pin 2 | VCC | Pin 2 |
| Pin 4 | GND | Pin 6 |
| Pin 5 | Reset  | Pin 5 |
| Pin 7 | SCK | Pin 3 |
| Pin 9 | MISO | Pin 1|

You may also refer to the image in the previous section to see the pinout for the Einsy's 32u2 ICSP header.

3) Run the following commands:

```shell
wget https://raw.githubusercontent.com/NicoHood/HoodLoader2/master/avr/bootloaders/HexFiles/HoodLoader2_0_5_Mega_atmega32u2.hex
avrdude -c usbasp -p m32u2 -U lfuse:w:0xEF:m -U hfuse:w:0xD8:m -U efuse:w:0xFC:m -U flash:w:HoodLoader2_0_5_Mega_atmega32u2.hex:i
```
Presumably this can be adapted to other programmers by changing the avrdude command.

4) Disconnect everything.  Connect power and USB back to your Einsy.  Run the following command if connected to a linux based system such as a Raspberry Pi:
`ls /dev/serial/by-id/`
The output should be:
`usb-NicoHood_HoodLoader2_Mega-if00`
5) You are now ready to print with improved communication stability.

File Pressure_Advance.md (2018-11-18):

In this guide we explain how to configure _PA_ on _Klipper_ using a specially crafted test object in just __one__ print.

# Quick and lazy (PLA-only)

Start with downloading the specially crafted [test object](files/klipper_PA_calibration_square_0.3mm_PLA_MK3.gcode) and printing it. As the file name suggests this is meant to be printed in _PLA_.

You should end up with a hollow rectangular object. Pay close attention to the corners. You will notice that at the very bottom of the object the corners are way overextruded, causing very noticeable bulging, with the bulging gradually disappearing as the height increases. You can feel the bulging with your finger if you move it over the corner.

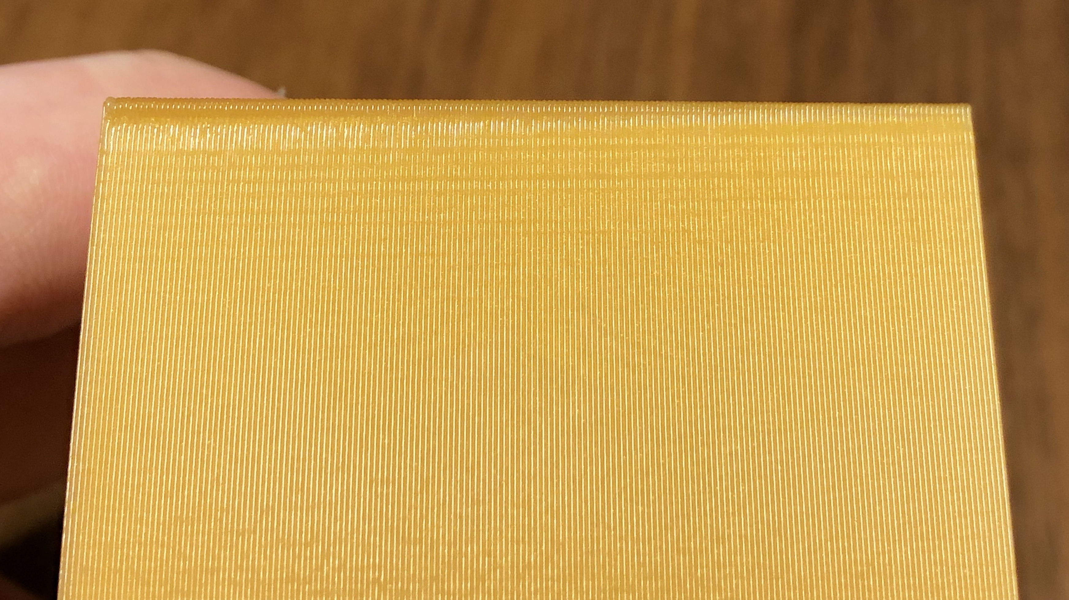
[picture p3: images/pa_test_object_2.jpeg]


You will also notice that the corners start deteriorating after passing a certain height - this will be easier to see on the internal features of the test print where the groove may start blending in and almost disappearing.

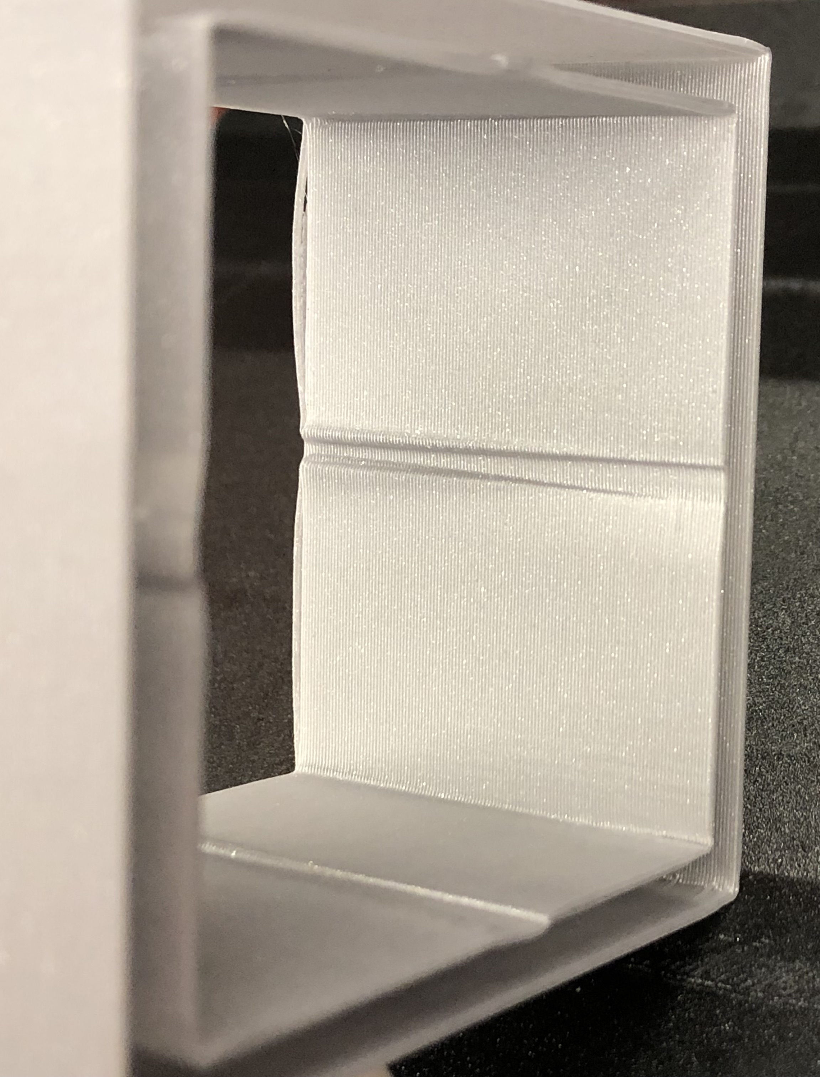
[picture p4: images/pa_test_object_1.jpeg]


Now try to find the height at which the bulge disappears but the corner is still sharp. Use a ruler to quantify this height.

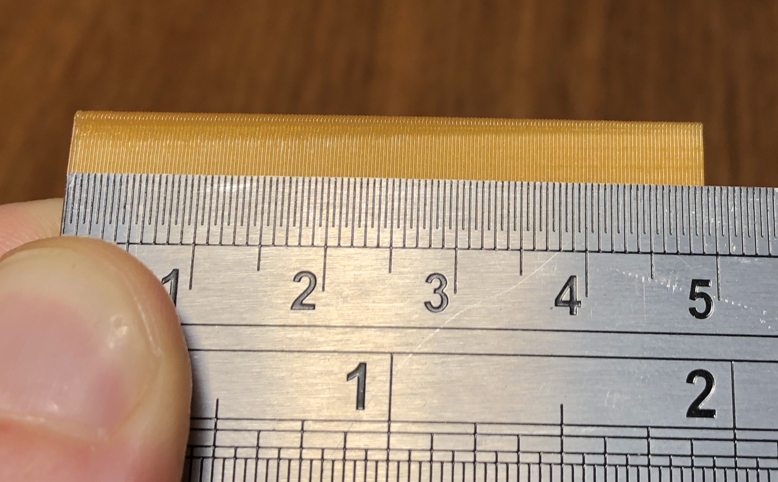
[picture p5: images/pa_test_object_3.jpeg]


In this example the optimim appears to be at `43mm`. Now all you have to do in order to obtain the _PA_ value is to multiply your optimal height (in millimeters) by `0.004`. For this example _PA_ is `43•0.004 = 0.172`.

Now edit your `Start G-code` under `Filament Settings / Custom G-code` in _Slic3r_ and put `SET_PRESSURE_ADVANCE ADVANCE=PA` there, where `PA` is the value you have calculated.

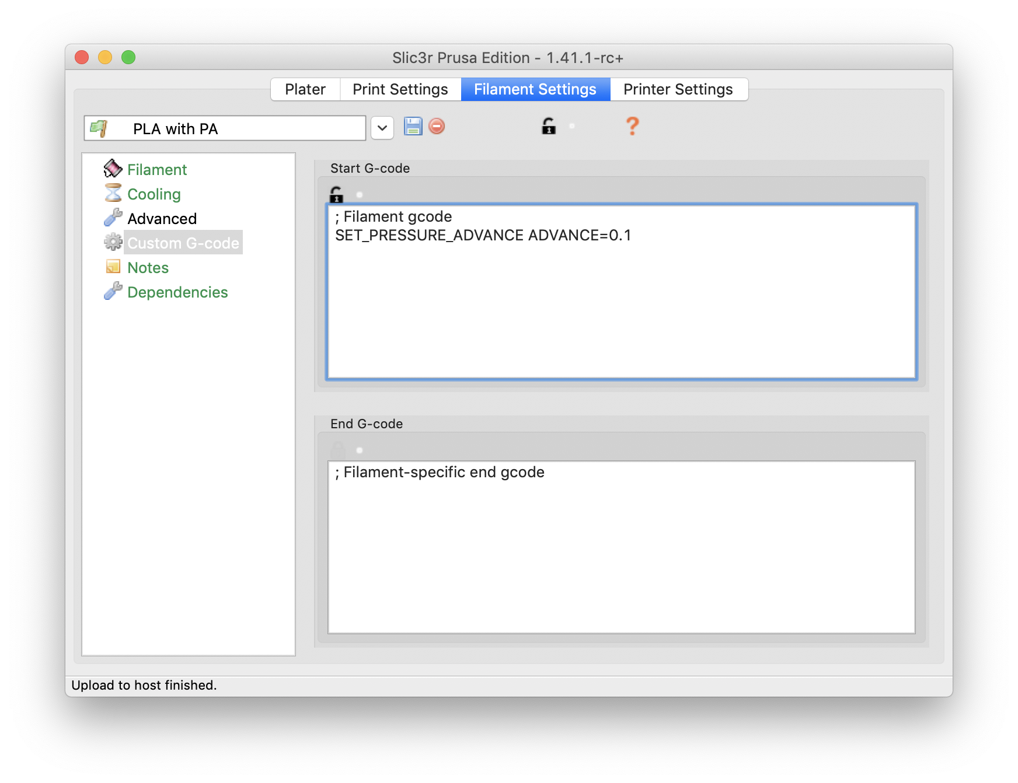
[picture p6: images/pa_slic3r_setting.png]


Please note that this setting is __per filament type__.

Finally, restart _Klipper_, either by issuing `sudo service restart klipper` on the console, or by issuing `restart` in _Octoprint_ terminal.

__This last step is very important.__

# Making your own test object for any filament (advanced)

The general idea is to gradually increase the _PA_ value as the print height increases.

Start with determining the parameters for _PA_ probing, in other words the range of _PA_ values to try out. For _PLA_ you probably want to go from `0` to `0.15`. For _PET_ you may want to start with `0.1` and go up to `0.2`. Please note that _PA_ values above `0.2` will stress the extruder too much and are likely to cause missed steps. Now you have two parameters: `START` and `MAX`.

Decide the total height of the test object (`HEIGHT`). Too low will make it impossible to find a good _PA_ value. Too high is a waste of filament and your time. We believe that `20-25mm` per `0.1` increase in _PA_ is optimal.

In the configuration below we are going to use the following values (so to arrive at the same _PLA_ test object as offered for download in the first section of this guide): `START=0`, `MAX=0.2`, `HEIGHT=50`.

- Get `square.stl` from _Klipper_ sources (you will find it under `docs/prints`) and load it in _Slic3r_.
- Scale it vertically to `HEIGHT` (`50mm`).
- Add the following to the end of your `Start G-code` under `Printer Settings / Custom G-code`:
  ```
  SET_VELOCITY_LIMIT SQUARE_CORNER_VELOCITY=1 ACCEL=500
  SET_PRESSURE_ADVANCE ADVANCE_LOOKAHEAD_TIME=0
  ```
- Add the following to `After layer change G-code`:
  ```
  {if layer_z > 0.4}SET_PRESSURE_ADVANCE ADVANCE={START + layer_z * ((MAX - START) / HEIGHT)}{endif}
  ```
  Please note that `START` and `((MAX - START) / HEIGHT)` are __numbers__. So for our _PLA_ values: `{if layer_z > 0.4}SET_PRESSURE_ADVANCE ADVANCE={layer_z * 0.004}{endif}`
- Set the following slicing settings:
  - Layer height to `75%` of your nozzle diameter (so `0.3mm` for the most common `0.4mm` nozzle).
  - `0` top solid layers.
  - `1` bottom solid layer.
  - `2` perimeters.
  - `0%` infill.
  - `100mm/s` printing speed (for everything save for the first layer).
- Slice and you are ready to go.

Your desired _PA_ value is `START + measured_height * ((MAX - START) / HEIGHT)`, or -- using the sample `START`, `MAX`, and `HEIGHT` values -- `measured_height * 0.004`.

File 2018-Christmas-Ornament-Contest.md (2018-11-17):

# 2018 Christmas Ornament Design Competition

## What is this?
The 602 Wasteland wants to have some friendly competition around the design of some sweet Christmas ornaments!

## Ornament Guidelines
While we don't want to stifle people's creative urges, we do have some design guidelines.

1. Shoot for a small to medium sized ornament, 3" or so. Ability to be scaled is awesome,
2. Should include an eyelet for string attachment for hanging,
3. Multi part entries are welcome, providing assembly is snap together or easily sourced (super glue),
4. Multi material entries are welcome, providing that a single filament option is made available as well,
5. Should be printable in PLA without much difficulty or specific hardware,
6. A photo of a completed ornament should be provided with your entry. This ensures you're providing a printable ornament and gives us something to put up for judging,
7. Ornament should be freely available on Thingiverse with a non restrictive license,
8. Multiple ornament designs are welcome; however, in the interest of keeping things fair, we ask that you photograph them together and enter them as one entry.

## Entry
Once you have completed your design, please get a photo and link to the Thingiverse post to your local 602 Wasteland admin. We have a behind the scenes channel to dump all this into, and we'll make it available for judging early in December! Entries are being accepted now!

## Prizes
The main prize of this competition is obviously the chance to show off your design skills; however, we're hoping the community will donate some small prizes (roll of filament, etc). Number of prize winners to be determined by how many prize contributions we receive.

## Judging
Judging will be decided by The 602 Wasteland community via the #announcements channel by reaction count. This will take the load off the admins for this and allow for them to enter as well.

## Have fun!

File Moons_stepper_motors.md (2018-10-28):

Prusa blogger Chris Warkocki experimented with and popularized use of stepper motors from Moons Industries as a replacement for the Prusa-supplied LDO steppers on the MK3. Chris has an excellent [write-up](https://prusacommunity.com/to-the-moons-and-back/) on this topic on his blog. My findings mirror Chris' experience; in general, don't expect a huge print quality improvement from this change, but the Moons motors do run quieter and cooler, and can supply more torque for a given amount of current. Given the issues with extruder heat creep, replacing the extruder motor only would be the best “bang for the buck”.

The Moons motor that is the closest replacement is the [MS17HD2P4100](https://www.moonsindustries.com/p/nema-17-standard-hybrid-stepper-motors/ms17hd2p4100-000004611110008899). This motor will require a custom cable, but otherwise is a drop-in replacement for the LDO stepper on the X and E axis. **On the Y axis, you will have an issue aligning the pulley because the flat on the Moons motor is not machined over the whole shaft** (you can get close by flipping the pulley around).

Finally, note that the Prusa firmware has tuned the motor driver settings for the LDO. Despite this, the settings seem to work OK with the Moons (although perhaps even better performance is possible). One thing to note is that extruder motor linearity correction (e-corr) does not work, so you will just want to disable this feature. Even with it disabled, however, results are similar to the optimized value with the LDO.

Finally, it's worth noting that LDO motors, makers of the stepper motors that Prusa current ships, has sent some samples out to various people of an updated stepper motor with similar characteristics to the Moons. Notably this motor doesn't have the issue with the shaft profile, so stay tuned for a possible better alternative.

Wiring the Motors
-----------------

The diagram below shows a known-good wiring for connecting the Moons to the Einsy. If you follow the wiring in the diagram, using wire with the same color, the order of the wire colors on the connector on the Einsy side will match that of the LDO motors.

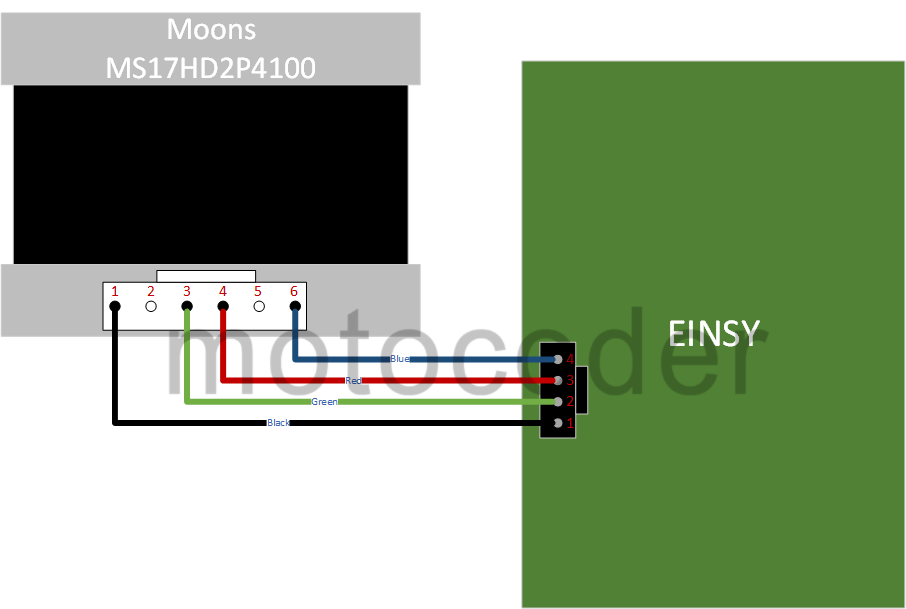
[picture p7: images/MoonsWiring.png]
<File:images/MoonsWiring.png>


Here is a picture showing the wire colors and the connector orientation on the back of a Moons motor.

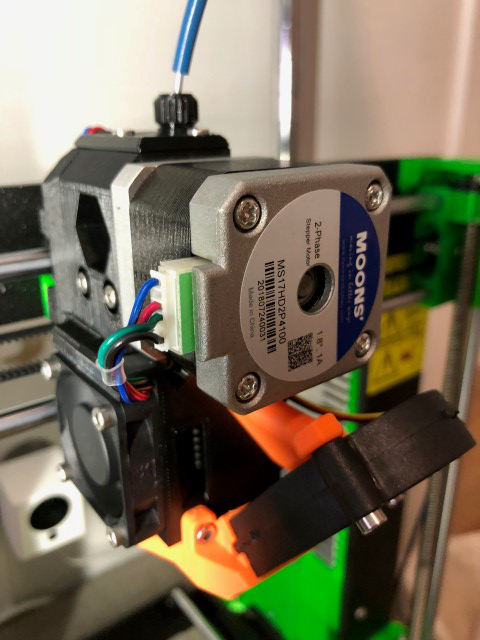
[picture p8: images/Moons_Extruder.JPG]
<File:images/Moons> Extruder.JPG File:Moons Extruder.JPG


Parts Needed
------------

| Item | Manufacturer | Part Number | Source |
|---|---|---|---|
| Connector housing on motor side of cable | JST | PHR-6 | [Digikey 455-1162-ND](https://www.digikey.com/products/en?keywords=JST%20PHR-6) |
| Connector pins on motor side of cable | JST | SPH-002T-P0.5S (Select variant per your wire gauge) | [DigiKey 455-1127-1-ND (24-30 gauge)](https://www.digikey.com/product-detail/en/jst-sales-america-inc/SPH-002T-P0.5S/455-1127-1-ND/527358) |
| Connector housing on Einsy side of cable | Molex | 50-57-9404 | [Mouser 538-50-57-9404](https://www.mouser.com/ProductDetail/538-50-57-9404) [Ultimachine “2.54mm 1x4 Connector & Positive Latch Housing Kit - 5 pack”](https://ultimachine.com/collections/electronics/products/2-54mm-1x4-connector-positive-latch-housing-kit-5-pack) |
| Connector pins on Einsy side of cable | Molex | 16-02-0097 | [Mouser 538-16-02-0097](https://www.mouser.com/ProductDetail/538-16-02-0097) |
| Wire | 24-gauge stranged (colors - red/green/blue/black) | Multiple Suppliers | I recommend you buy cables with JST connectors similar to those described below |

Alternatively, you can buy **pre-made cables with the JST (motor side) connectors on one end**. You will have to replace the connector on the other end, and you may have to pop pins out of the JST connector to re-order things (if you want the colors to match as described above), but it at least saves you from having to crimp and assemble this connector. Amazon.com sells [this set of cables](https://www.amazon.com/gp/product/B01JM9ML38/ref=oh_aui_search_detailpage?ie=UTF8&psc=1) which are known to work.

The Molex **crimp tool** is quite expensive, but several people, myself included have reported success with this **IWISS tool** available on [Amazon.com](https://www.amazon.com/gp/product/B00OMM4YUY/ref=oh_aui_search_detailpage?ie=UTF8&psc=1).

The following table provides the length of the stock motor cable wires on the MK3. This is measured from the motor body to the start of the connector housing. If you plan on twisting the cable like those on the Prusa-supplied motors, make sure you do that before measuring.

| Axis | Length (mm) |
|---|---|
| E | 720 |
| X | 365 |
| Y | 510 |
| Z (short)| 255 |
| Z (long) | 555 |

**One last thing** - If you're pretty sure you are going to keep the Moons motors, I recommend you pop the pins out of the connector on the LDO motor, and remove the little yellow plastic wire labels. Then you can put these on the new cables you make.

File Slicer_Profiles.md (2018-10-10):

This page contains profiles (configuration files) for various slicer software, such as Simplify3d, Slic3r / Slic3r PE, Cura, etc.

| Printer | Slicer | Link | Description |
|---|---|---|---|
| MK3 | Slic3r PE | [MK3 Pretty PLA Profile.ini](https://www.facebook.com/groups/Prusai3users/937992506385231/) | Pretty PLA Profile from Chris Warkocki |
| MK3 | Slic3r PE | [Benchy profiles](https://github.com/PrusaOwners/test-tools-and-objects/tree/master/tools/slicers/Slic3rPE/kwaad2/Benchy) | Profiles from Discord user kwaad2 for generating test benchies |
| MK3 | Slic3r PE | [0.6mm Production Profiles](files/BuzzAldrin_06mm_PETG_Config_Bundle.ini) | Contains PETG and PC profiles for 0.6mm nozzles tuned for very strong and rigid parts from BuzzAldrin. |
| MK3 | Slic3r PE | [RealFilament PETG Configs](https://github.com/ManuGithubSteam/RealFilamentSlic3rSettings) | Contains PETG Profiles for Filament from REAL Filement brand from ManuGithubsteam. |
| MK3     | Slic3r PE | [FFF World FlexiSmart TPU Configs](https://github.com/ManuGithubSteam/RealFilamentSlic3rSettings) | Contains TPU Profiles for FlexiSMART Filament from FFF World brand from ManuGithubsteam. |

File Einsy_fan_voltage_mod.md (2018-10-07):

High-performance 5 volt fans with tachometer outputs are hard to find. 12 volt fans are commonplace and 24 volt fans are plentiful-enough. So here's a mod to allow an Einsy to natively drive other-voltage fans.

### Top side board modifications
1. Remove FB23 to disconnect the 5 volt supply to the fans. Red in diagram.
2. Remove R9, R16 to avoid reverse biasing the LEDs and blowing them up. Red in diagram.
3. Replace R30 and R33 with a [Schottky diode](https://www.digikey.com/product-detail/en/comchip-technology/CDBQR70/641-1281-1-ND/1973560) to protect the ATMEGA2560 from poorly-behaved fans. Orange in the diagram.
4. Replace R28 and R29 with [10k resistors](https://www.digikey.com/product-detail/en/samsung-electro-mechanics/RC1005F103CS/1276-3431-1-ND/3903534) to allow a logic pull-up for open-drain fans, but without burning up the resistor. Pink in the diagram.
5. Replace R44 and R55 with (100 ohm resistors)[https://www.digikey.com/product-detail/en/yageo/RC0402FR-07100RL/311-100LRCT-ND/729474] to allow for faster discharge of the filter capacitor. This allows you to read high-RPM fans' tachometer outputs. Also pink in the diagram (oops, sorry).
6. Replace C42 and C43 with [4.7 nF capacitors](https://www.digikey.com/product-detail/en/samsung-electro-mechanics/CL05B472KB5VPNC/1276-6576-1-ND/5961435), also for high-RPM fan tachometer compatibility. It's unclear why so much filtering was put in the design in the first place. Purple in the diagram.
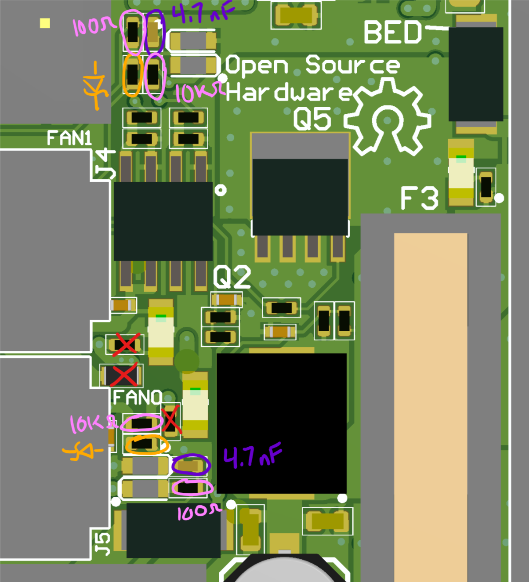
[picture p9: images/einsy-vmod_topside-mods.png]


### Bottom side board modifications
1. Connect the center pin of one of the fan headers to the voltage with which you would like to drive the fans. In the diagram, that's the board input voltage (24 volts on MK3). Use insulated wire. I like [solderable magnet wire](https://www.amazon.com/Remington-Industries-24SNSP-125-Enameled-Diameter/dp/B076C9Q19T/) so I that I can strip it in-place with my soldering iron.
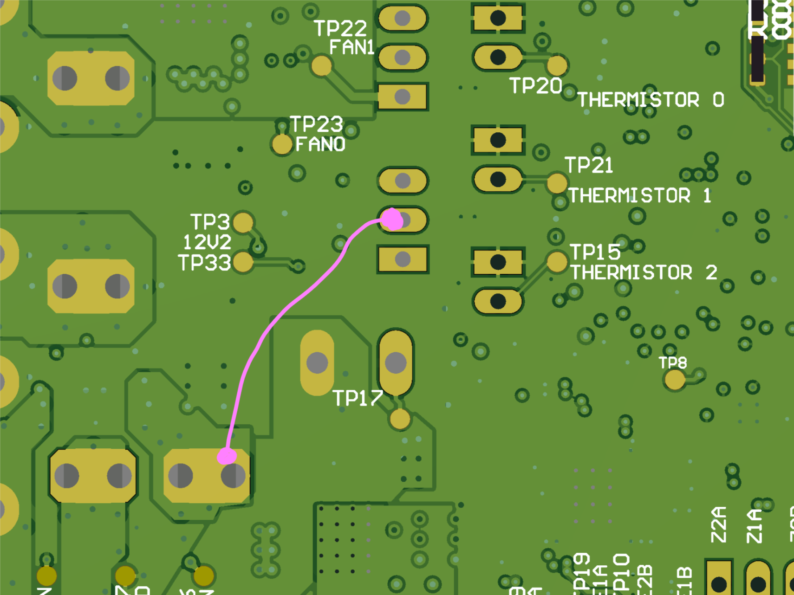
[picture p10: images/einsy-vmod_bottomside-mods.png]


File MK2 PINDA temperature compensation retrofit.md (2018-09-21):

# MK2  to MK2E conversion:
TODO: Bed calibration fails with current firmware that I have been working on.
TODO: Backport gcodes M860 and M861 to MK2 firmware. Using MK3 firmware branch and modding it to work with MK2's bed points for calibration has proven to be very difficult. As it goes along the probing points in the X direction, it moves in the Y direction, even though all the points are in a straight line as defined in the firmware.

This guide explains how to retrofit a temperature compensating PINDA probe to the Prusa i3 MK2 (and MK2S). The probe triggering distance will drift a significant amount inside of a heated enclosure if no temperature compensation is fitted.

## Firmware:
We need to update the firmware to read the temperature sensor inside the PINDA V2 probe. Alternatively you can use the V1 probe, but you will have to add a thermistor in your own creative way, and you will also need to define the type of thermistor in the firmware if it is not type 1 (1 is 100k thermistor - best choice for EPCOS 100k (4.7k pullup)).

Install [this firmware](https://github.com/TTN-/Prusa-Firmware/blob/MK3/README.md).

# Hardware:

### PINDA V2 users:
Connect white wire, which is the thermistor lead on the PINDA V2 probe to T1 thermistor plug's signal pin on your rambo board. If its unclear, [see the pictures here](https://shop.prusa3d.com/forum/others-archive--f82/is-the-mk3-pinda-v2-compatible-with-the-mk2-rambo--t14786.html)

### PINDA V1 users:
If you're cheap like me, you attach a 100k thermistor to your pinda probe in some sort of thermally conductive manner. [Here is how I did it](https://imgur.com/a/XO0Dp0j)

Connect the thermistor to plug T1.

# Calibration:
Gcodes:
M860 - Wait for PINDA thermistor to reach target temperature.
M861 - Set / Read PINDA temperature compensation offsets
G75  - display current calibration

The LCD menu has a PINDA autocalibration entry under Menu -> Calibration -> Temp. calibration

Alternatively you can follow [Crzcrz's calibration guide](https://github.com/crzcrz/prusaowners/blob/master/First_layer_and_PINDA_temperature_calibration_with_calipers.md)

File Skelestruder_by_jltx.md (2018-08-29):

Skelestruder is a custom 3.5:1 (or 4:1) geared extruder with mostly printable parts for the Prusa Mk3, designed by JLTX

Link to parts <https://www.thingiverse.com/thing:2845416/#files>

Improved instructions &gt;&gt;&gt; [Skelestruder Assembly](https://github.com/PrusaOwners/prusaowners/wiki/Skelestruder_Assembly)

Sortable, filterable spreadsheet with part/file names, and recommendations for material and color is available [here](https://docs.google.com/spreadsheets/d/19_bpOaFNy87UGM9JST4Ibljp2dwbiq5kfsb0czmPD2Y/edit?usp=sharing).

### 3d renderings with labeled parts

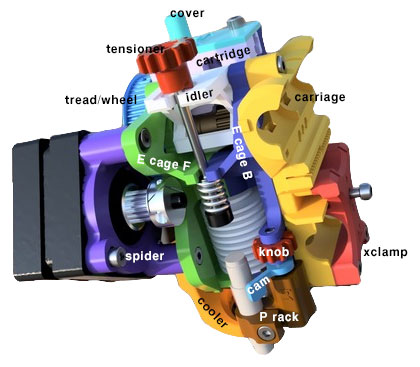
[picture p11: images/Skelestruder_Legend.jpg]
<File:Skelestruder> Legend.jpg File:Skelestruder Legend.jpg


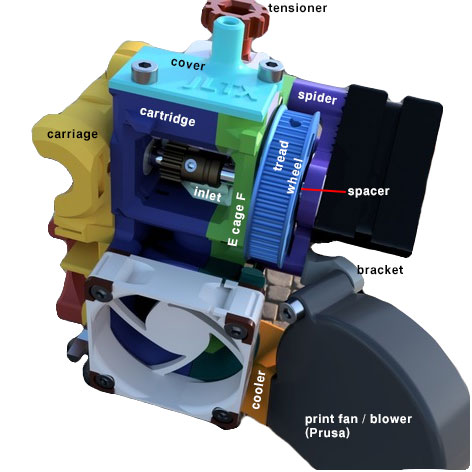
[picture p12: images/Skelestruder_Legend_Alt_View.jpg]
<File:Skelestruder> Legend Alt View.jpg File:Skelestruder Legend Alt View.jpg


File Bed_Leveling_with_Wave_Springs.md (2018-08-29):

The Prusa firmware has an auto-bed leveling feature. This feature uses a probe that is attached to the extruder assembly to measure the approximate height of the probe above the bed service. Since the probe is a fixed and known distance from the nozzle, this value serves as a proxy for the nozzle height above the bed. The Prusa MK3 firmware probes this height at 9 points across bed in a procedure that you have no-doubt observed before prints and during the printers initial calibration process. The firmware than takes these 9 points and extrapolates them into a 49-point matrix. This matrix is used during print to make micro-adjustments to the nozzle (Z) height to partially compensate for the bed not being perfectly level.

Although this electronic adjustment is a wonderful feature, and does improve first-layer, and hence print, quality, it is not as good as having a mechanically level bed. As it turns out, there is a simple way we can make the bed much closer to a perfect level, and in the process make life for the Prusa firmware much easier, and give overall better results.

To achieve this, we will insert springs between the spacers and the MK52 heatbed, and then use screw tension to compress each spring the appropriate amount to make the bed approximately level. There are two options for the springs needed for this task, so let's start by discussing each, and where to get them.

Before we get started, I should mention that before going through the leveling procedure, it is very important to ensure that your z-tops and Y rod holders are as parallel as possible (TODO: Need link describing how to do this).

Wave Springs
------------

Wave springs are visually similar to washers. They have a bent appearance and under load tend to flatten out. They are similar to a small spring you can adjust. By installing these between the Y carriage and the bed of any 3D printer and using a program such as Prusa Mesh Bed Visualizer (see below for details).

The wave springs many people are using are available from McMaster-Carr, part number [92168A101](https://www.mcmaster.com/#92168a101/)

Multiwave Springs
-----------------

Amazon.com sells a product they call “Multiwave Washers”. They look like small springs, but if you look closely appear more like multiple wave washers stacked on top of each other. They provide a larger range of adjustment than the Wave Springs described above. These springs are available [here](http://a.co/5iHSq7o). In case the product link changes, the product name is “Multiwave Washers, 17-7PH Material,Compression Wave Spring，CM06-M3, Metric, 4mm ID, 6mmOD, 0.15mmThick,Material width0.61mm,5 Turns, Free height2.54mm, 9.09 N/mm Spring Rate, 12N Load Capacity”.

Installing the Springs
----------------------

The process to install the two types of springs is different, so we'll go over each independently. By the way, if you're wondering which spring to choose, most people find the Multiwave springs to be a better option. They are also considerably easier to install if you utilize the “straw technique” discussed below. To install the single wave springs, you first slide the spring over the appropriate hole, and then using the pliers move the spacer into place. Lift up on the spacer so that you clear the spring and don't push it out of the way. Once you've achieved this feat of manual dexterity, quickly insert something like a small hex wrench to hold everything in place while you get one of the bed screws. Carefully remove the hex wrench, and replace it with the screw. Screw it down just slightly - just enough so that you're sure it won't come out, and then move onto the next position. We don't want to tighten the screws too much now, because we need to be able to lift the bed up to clear the spring when we are inserting a spacer.

If you find this is too much for you, one trick you can do is to use a little dielectric grease (sometimes called bulb grease) to help hold the washer in place. Dielectric grease is a good choice because it's not electrically conductive, it's stable under the temperatures generated by the heatbed, and it's very viscous.

### Installing Wave Washers / Springs

The process to install these springs is simple, but it requires a bit of manual dexterity. Basically you To install the wave springs, you place a washer flat against the frame above the

### Installing the Multi-Wave Springs

It can be a bit of a challenge to install these springs. It is almost impossible to hold the spring on the waster, insert it under the screw hole in the heatbed, and then insert a screw through all three. However, there is a technique you can use that makes it a relatively simple, if tedious, process.

First you should install the spring, spacer, and screw in the center hole. The best method I have found to do this is to insert the screw through the heatbed, add the spring and then the spacer, and then put a small amount of grease on the bottom of the screw to cause all 3 components to stick together. Carefully align the heatbed over the center hole in the frame, using the other holes as milestones. Screw the center screw in slightly. Ok, this was the hardest part.

For the remaining screws, you will need a large straw similar to the kind they have at McDonalds. Cut the straw into 5mm sections. You will need 8 of them. If you can't find a suitable straw in you area, an alternative would be heat shrink tubing (one user heats the heat shrink to really tightly retain the spring and spacer as an assembly).

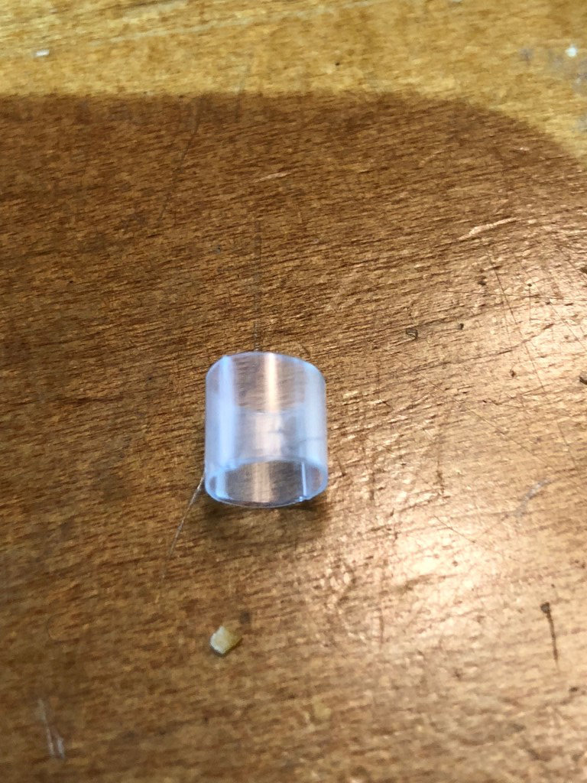
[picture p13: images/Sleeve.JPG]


To install a spring, first place the sleeve (piece of straw) on the spacer. Don't push the sleeve all the way down, however; leave enough sticking up to hold one of the springs. Insert a spring into the sleeve, so that it is resting on top of the spacer and captured by the sleeve.

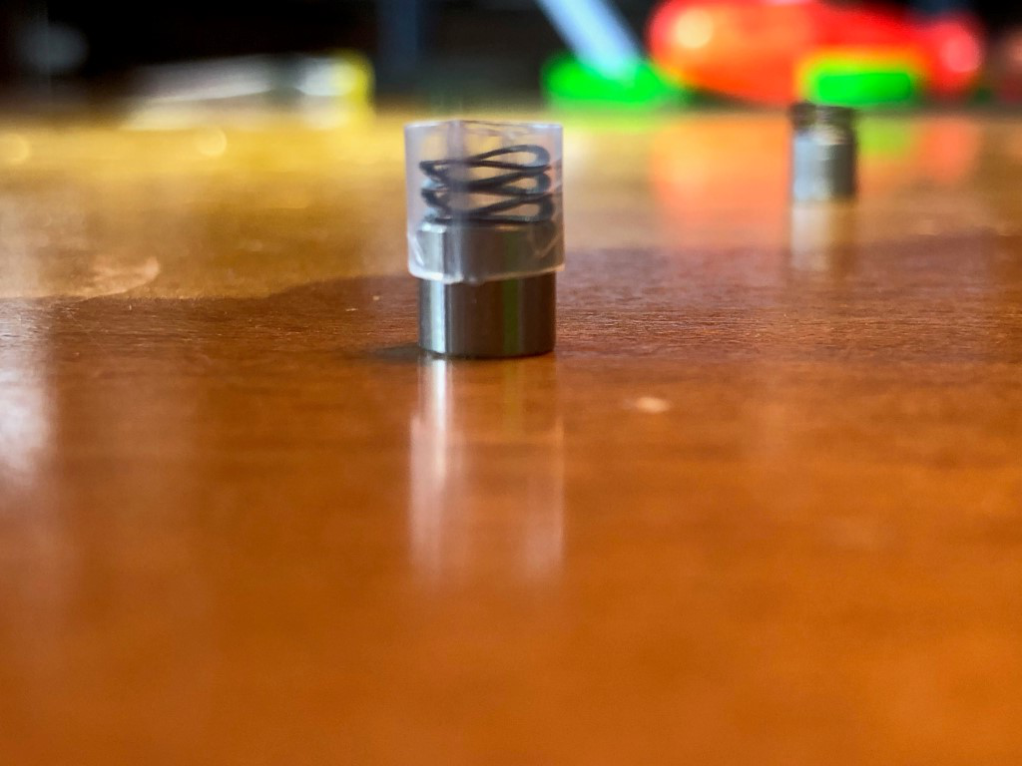
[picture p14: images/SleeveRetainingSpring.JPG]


Now, take a pair of pliers and grip the spacer near the top so you are holding both the sleeve and the spacer.

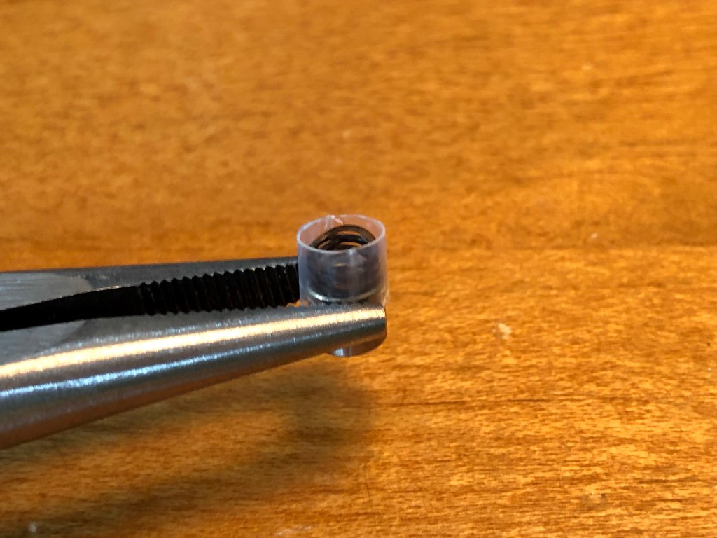
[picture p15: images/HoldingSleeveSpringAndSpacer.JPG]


Finally, place the sleeve, spacer, and spring in place on the frame over one of the holes. Align the heatbed if necessary (you can use the other holes to do a visual alignment check). I like to insert a small hex wrench into the hole to lock in the alignment until I can grab a screw. Insert a screw and tighten it a turn or two. Repeat for the remaining 7 spacers.

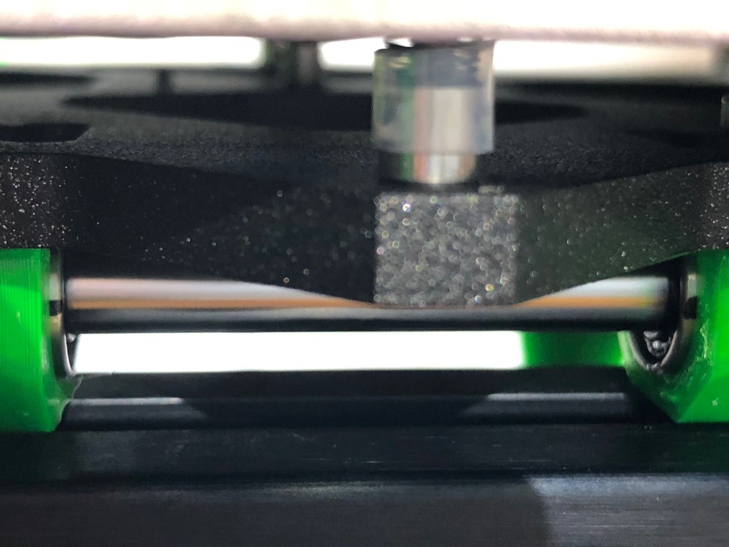
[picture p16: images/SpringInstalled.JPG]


If you cut the sleeves to the size mentioned above, they shouldn't interfere with anything. However, if you want to remove them - because you're concerned about plastic underneath the heatbed, or whatever - you can take an exacto knife and cut them apart, and then remove them with pliers. Or... use a straw with a diameter slightly smaller than the spacer. Cut it first, then wrap it around the spacer and spring. After fixing it with the screw, grab the sleeve with the pliers and it should just pop off.

All done! Now follow the steps discussed below to mechanically level your bed.

Leveling Your Bed
-----------------

Now that we have the springs in place, we are ready to perform the actual bed leveling procedure. You could tell the printer to perform the bed leveling procedure by sending it a g-code (G80), and then read the values back out using another g-code (G81), and then use the returned values to figure out which screws to tighten or loosen. But it's considerably easier if you have some software to do this task.

The software we will discuss here is a plug-in for the popular Octoprint software. Several of the Discord users collaborated on a [Octoprint plug-in](https://github.com/PrusaOwners/OctoPrint-PrusaMeshMap) that shows a representation of the mesh bed leveling points, and the interpolated contour that the Prusa firmware uses. This plugin requires stock Prusa firmware as of right now, with Klipper support hopefully coming soon. Indications are that the Klipper support will be even better because it will measure more than 9 points!

Some sample output from this plug-in can be seen in the screenshot below.
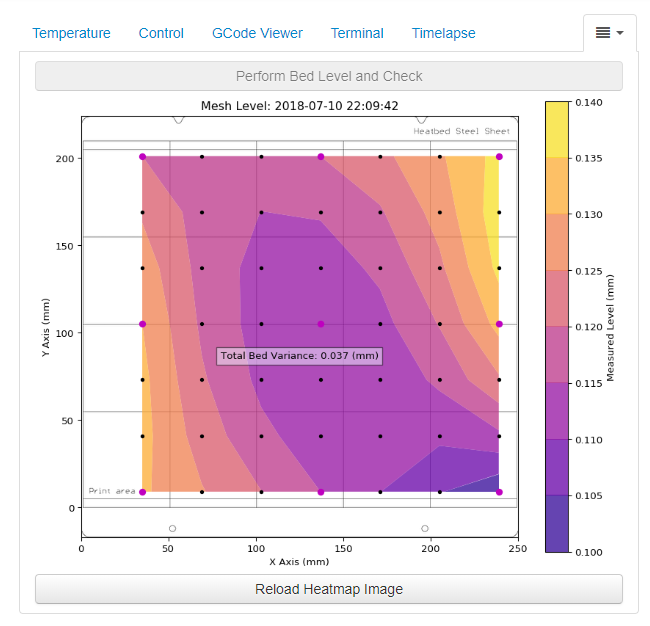
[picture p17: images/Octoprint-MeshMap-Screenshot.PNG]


You use this plug-in to run the mesh bed leveling routine, view the generated contour map, make leveling adjustments by turning one or two of the bed screws, and then iterate on this process until you have something you are satisfied with.

To determine which screws to turn, and how much to turn them, first start by putting all the screws at a position where the screens are approximately 50% compressed. It's not critical to be exact here; we are just trying to ensure we have some margin to adjust each screw in each direction (tighter or looser). Use the plug-in to perform a bed level check. Wait for this to complete, and then wait a few more seconds for the plug-in to generate the updated image (it's pretty slow), then press the “Reload Heatmap Image” button. You should see a graph similar to the one shown above.

Note the “Total Bed Variance” value in the center of the graph. This tells you how far you are off level. The pink dots in the graph represent the actual measured values; the black dots are the Prusa interpolated values. Using the pink dots as your milestones, note the color around them. You are looking to find the one or two screws that are most extreme (too low, or too high). You will adjust those screws, and which screws they are may change with each iteration. Remember that the thread pitch on these screws is 0.5mm per turn. So you may have to turn them a half turn or so at first, but after that you will quickly reduce the amount you are turning the screws.

Repeat the mesh map calculation and adjustments until you are happy with the results. I recommend not trying to get better than about 0.03mm. The Pinda sensor is not much more accurate than that, and in addition the bed will vary as you heat it to different temperatures due to thermal expansion.

### Mesh Leveling G-Code

The Octoprint plug-in comes with some default g-code to perform the bed measurements. However, if you want a more accurate measurement, you should modify it to do the following:

1.  Measure the bed when the PINDA probe is at some consistent temperature (35C is the lowest value I would recommend).
2.  Make the measurements with the bed at some consistent temperature, ideally something close to the temperature you most frequently print at.

**For those running Prusa firmware 3.3.0 or higher**, you can use the script below. This script first waits for the PINDA to cool down to 35C or lower, than heats the bed up and waits for it and the PINDA probe to reach a desired temperature, then runs the mesh bed measurement and outputs the results.

```G-code
G28 W ; home all without mesh bed level
G0 X50 Y50 Z70 F1500 ; Raise PINDA in case cooling is needed
M860 S35 ; Wait for PINDA <= 35C
M190 S60; set and wait for bed temp
M104 S170  ; set nozzle temp
G0 X50 Y50 Z0.15 F1500 ; this is a good PINDA heating position
M860 S35 ; wait until PINDA is >= 35C
G80 ; mesh bed leveling
G81 ; check mesh leveling results
G4 ; wait
M104 S0 ; turn off temperature
M140 S0 ; turn off heatbed
G0 X50 Y50 Z70 F1500 ; Raise PINDA back for next iteration
```

**For those running Prusa firmware earlier than 3.3.0**, you can use the script below. This script is identical to the one above, except that it does not first wait for the PINDA probe to cool down (because the firmware does not support this feature).

```G-code
G28 W ; home all without mesh bed level
G0 X50 Y50 Z70 F1500 ; Raise PINDA in case cooling is needed
M190 S60; set and wait for bed temp
M104 S170  ; set nozzle temp
G0 X50 Y50 Z0.15 F1500 ; this is a good PINDA heating position
M860 S35 ; wait until PINDA is >= 35C
G80 ; mesh bed leveling
G81 ; check mesh leveling results
G4 ; wait
M104 S0 ; turn off temperature
M140 S0 ; turn off heatbed
G0 X50 Y50 Z70 F1500 ; Raise PINDA back for next iteration
```

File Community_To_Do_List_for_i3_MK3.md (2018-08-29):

To Be Fixed
-----------

### Inconsistent Extrusion

Inconsistent Extrusion is still not fixed. Many details can be seen at [Github Issue \#602](https://github.com/prusa3d/Prusa-Firmware/issues/602).

To Be Improved
--------------

### Klipper

#### Done

-   Basic Configuration
-   Linear Correction
-   Compatibility with Brigandier's PrusaMeshMap plugin
-   Support for M117, LOAD_FILAMENT, and UNLOAD_FILAMENT gcodes

#### BETA

N/A

#### ALPHA

-   Mesh Bed Leveling - See [Klipper#configuring-mesh-bed-leveling](Klipper#configuring-mesh-bed-leveling "wikilink")
-   Pinda Drift Compensation - See [Klipper#alpha-probe-temperature-compensation](Klipper#alpha-probe-temperature-compensation "wikilink")

#### Todo (ordered by priority)

-   Mesh Leveling Alpha 2 (Parameterized Variables, support larger probe sample and bicubic interpolation, custom gcode to report json serialized probe points to the terminal for Brigandier's plugin)
-   Live-z support
-   Fan sensors
-   Filament sensors
-   Use z tops to tram x axis (ram into top)
-   Support for homing z axis at center of bed naively rather than through G0
-   Octoprint plugin supporting Klipper installation and upgrades
-   Support for display connected directly to the Pi

### Skelestruder

#### Done

@leefla -&gt; write up better instructions already! :-)

#### Todo (ordered by priority)

### Bed Leveling Modifications

Mesh bed leveling is nice, but ultimately it leaves parts with curved bottoms (or curved all the way through, if no Z fade is present) or skew. This can be mitigated by leveling the system properly.

#### Done

-   Octoprint Plugin has been made for quickly understanding bed level issues.
-   Wave springs under the bed standoffs allow for bed curvature correction.

#### Todo

-   Create Y axis rod mounts that allow leveling
-   Create Z stepper mounts that allow leveling
-   Create Z axis endcaps that allow leveling

Documentation
-------------

@jltx write up SCAD -&gt; STEP flow

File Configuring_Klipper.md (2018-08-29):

Configuring Klipper is actually very easy to do. All changes happen on the host computer (such as the Pi) inside of the printer.cfg file in your home directory. An example config file would look like this:

```
# This file contains pin mappings for Prusa i3 MK3 printers. To use
# this config, the firmware should be compiled for the AVR atmega2560.

# See the example.cfg file for a description of available parameters.

[probe]
pin: PB4
# TODO: Just an estimate/test z_offset.  The offset will increase as the temperature
# increases.  The thermistor in the PINDA can be used to calibrate a set of values
# to change the offset based on PINDA temperature
z_offset: .15 
speed: 5.0
#activate_gcode:
#deactivate_gcode:

[stepper_x]
step_pin: PC0
dir_pin: !PL0
enable_pin: !PA7
step_distance: .005
endstop_pin: tmc2130_stepper_x:virtual_endstop
position_endstop: 0
position_max: 255
homing_speed: 50.0
homing_retract_dist: 5.0

[tmc2130 stepper_x]
cs_pin: PG0
microsteps: 32
run_current: .282
hold_current: .1
sense_resistor: 0.220
diag1_pin: !PK2

interpolate: True
#stealthchop_threshold: 50 
driver_SGT: 3
driver_IHOLDDELAY: 8 
driver_TPOWERDOWN: 30 
driver_BLANK_TIME_SELECT: 2 
driver_TOFF: 3 
driver_HEND: 1 
driver_HSTRT: 5
driver_PWM_AUTOSCALE: True
driver_PWM_FREQ: 2
driver_PWM_GRAD: 2
driver_PWM_AMPL: 230

# TODO: Check the endstop and min position. The build area may be more than 4mm away
# from where the y-axis actually homes to
[stepper_y]
step_pin: PC1
dir_pin: PL1
enable_pin: !PA6
step_distance: .005
endstop_pin: tmc2130_stepper_y:virtual_endstop
position_endstop: -2.2
position_max: 212.5
position_min: -4.0
homing_speed: 50.0
homing_retract_dist: 5.0

[tmc2130 stepper_y]
cs_pin: PG2
microsteps: 32
run_current: .348
hold_current: .1
sense_resistor: 0.220
diag1_pin: !PK7
interpolate: True
#stealthchop_threshold: 50 
driver_SGT: 3
driver_IHOLDDELAY: 8 
driver_TPOWERDOWN: 30 
driver_BLANK_TIME_SELECT: 2 
driver_TOFF: 3 
driver_HEND: 1 
driver_HSTRT: 5
driver_PWM_AUTOSCALE: True
driver_PWM_FREQ: 2
driver_PWM_GRAD: 2
driver_PWM_AMPL: 235

[stepper_z]
step_pin: PC2
dir_pin: !PL2
enable_pin: !PA5
step_distance: .0025
endstop_pin: probe:z_virtual_endstop
#endstop_pin: tmc2130_stepper_z:virtual_endstop
position_endstop: 0.75
position_min: -0.5
position_max: 210
homing_speed: 13.3333

[tmc2130 stepper_z]
cs_pin: PK5
microsteps: 16
run_current: .53
hold_current: .15
sense_resistor: 0.220
diag1_pin: !PK6
interpolate: True
#stealthchop_threshold: 50 
#driver_SGT: 4
driver_IHOLDDELAY: 8 
driver_TPOWERDOWN: 30 
driver_BLANK_TIME_SELECT: 2 
driver_TOFF: 3 
driver_HEND: 3 
driver_HSTRT: 6
driver_PWM_AUTOSCALE: True
driver_PWM_FREQ: 2
driver_PWM_GRAD: 4
driver_PWM_AMPL: 200

[extruder]
step_pin: PC3
dir_pin: PL6
enable_pin: !PA4
step_distance: .00357142857143
nozzle_diameter: 0.400
filament_diameter: 1.750
# TODO: The max extrude cross section is increased for the purge line, but in theory
# its probably a bad idea to have it this large, as its purpose is to catch poorly sliced
# objects that extrude way too much for small moves
max_extrude_cross_section: 50.0
# Allows to load filament and purge up to 500mm
max_extrude_only_distance: 500.0
max_extrude_only_velocity: 120.0
max_extrude_only_accel: 1250.0
pressure_advance: 0.04
pressure_advance_lookahead_time: 0.01
# Pressure advance
heater_pin: PE5
sensor_type: ATC Semitec 104GT-2
sensor_pin: PF0
control: pid
pid_Kp: 16.13
pid_Ki: 1.1625
pid_Kd: 56.23
min_temp: 0
max_temp: 305

[tmc2130 extruder]
cs_pin: PK4
microsteps: 32
run_current: .514
hold_current: 0.1
sense_resistor: 0.220
diag1_pin: !PK3
interpolate: True
#stealthchop_threshold: 50 
#driver_SGT: 3
linearity_correction: 1.06
# This is linearity correction, similar hopefully same as prusa firmware.
driver_IHOLDDELAY: 8 
driver_TPOWERDOWN: 30 
driver_BLANK_TIME_SELECT: 2 
driver_TOFF: 3 
driver_HEND: 2 
driver_HSTRT: 5
driver_PWM_AUTOSCALE: True
driver_PWM_FREQ: 2
driver_PWM_GRAD: 4
driver_PWM_AMPL: 240

[heater_bed]
heater_pin: PG5
sensor_type: EPCOS 100K B57560G104F
sensor_pin: PF2
control: pid
pid_Kp: 126.13
pid_Ki: 4.3
pid_Kd: 924.76
min_temp: 0
max_temp: 125

[heater_fan nozzle_cooling_fan]
pin: PH5
heater: extruder
heater_temp: 50.0
fan_speed: 1.0

# Part Cooling Fan
[fan]
pin: PH3

[mcu]
serial: /dev/ttyACM0

[display]
lcd_type: hd44780
rs_pin: PD5
e_pin: PF7
d4_pin: PF5
d5_pin: PG4
d6_pin: PH7
d7_pin: PG3

[printer]
kinematics: cartesian
max_velocity: 200
max_accel: 1500
max_z_velocity: 15
max_z_accel: 750

# Keeps Debug LED off / not floating
[static_digital_output debug_led]
pins: !PB7 
```

The config file is broken up into sections by \[\]. Under each of these sections is relevant configurations. For example, under \[tmc2130 stepper_x\] you can change settings such as running current, microstepping, distance per step, and homing speeds.

To apply changes made in the config file, issue the following command to Octoprint under the Terminal tab: RESTART

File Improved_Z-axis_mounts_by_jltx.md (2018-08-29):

Parts
-----

[Improved Z-axis mounts by JLTX on Thingiverse](https://www.thingiverse.com/thing:2779123)

[Prusa Mk3 official part files - including R2 X-carriage ends](https://www.prusa3d.com/download-printable-parts-stl-mk3)

Improved installation instructions - WIP
----------------------------------------

**Z-Mount removal**

1. Move Z axis to top (either using Octoprint, or by hand after power disconnected)

2. Disconnect power from printer

3. Lean the printer onto it's back edge, support the top of the printer frame to keep it flat (I just used a box), while holding the bed to the front (to avoid squashing the heated bed cable)

4. Use a support to stop the bed sliding backwards. (another small box may suffice)

5. Remove the bolts holding each Z Motor to their mounts

6. Remove the cable ties securing the Z Motors (do NOT attempt to remove Z motors from mounts completely yet).

7. Slide Z Motors down slightly to expose Z Motor Mount screws. (with the Z screw-rods still attached to the X-carriage)

8. Remove Z Motor mount screws

9. Slide the motor mounts down slightly, and release the smooth z rods from both top and bottom mounts, but NOT from the X carriage.

10. Twist the Z Motor screw-rods by hand to detach from the X-axis ends.

11. The Z motor mounts can now be removed by sliding them over the end of the Z screw-rods

12. The Z top mounts can also be removed at this time

If you are not also replacing the X Carriage ends then we can just follow the process in reverse to install the new Z mounts. That will be covered below. Continue on if you are also replacing the X Carriage ends

**Replacing X-carriage ends**

1. Rest the Z motors on the floor. (The left motor cables may not reach, so it may be propped up on the chassis)

2. Remove the left-front screw holding the black t-nut to the X-carriage idler end. Be careful to remove, and not lose, the small nut. (I recommend securing it back to the screw)

3. Remove the other screw holding the black T-nut. Note that after removing the screw, the nut recessed inside the hole will be unsecured. (It is unlikely to fall out, but be careful just in case)

4. Remove the black T-nut from the X-carriage idler end

5. Remove the screws securing the x-axis pulley from the idler end, and then free the pulley. (note that the nylock nut on the back of the idler is likely to stay secured, but be careful just in case it falls out unexpectedly)

6. Slide the extruder towards the right side since it will be used to support the ends of the X rods

7. Holding the ends of the X rods, gradually tease the X-carriage idler end from the rods by wriggling it free. (keep the Z rod in the X-carriage idler at this time, unless you also plan to replace the linear bearings)

8. Use pliers to remove the lock nut from the back of the idler end, and put it in the replacement X-carriage idler part (it'll be a tight fit. If you can't get it to go in then use the bolt to pull it through, but don't over-tighten, then remove the bolt again.

9. Remove the captive nut from inside the X-carriage idler, that was used to retain the T-nut. Using a fine point Jewelers screwdriver to free it works, but it is fiddly (secure to the screw to avoid losing it)

10. If re-using the existing linear bearings, then use an ultra-fine point 'Sharpie' (permanent marker) pen to draw a line along the linear-bearings via the gap in the X-carriage idler. This helps to ensure that they are aligned similarly when installing in the replacement part.

11. Remove the linear bearings from the X-carriage idler.

11a. If you are not replacing the bearings then it is recommended to try to remove them with the them still on the Z rod to avoid the chance of losing individual ball bearings. This may be done by using a long thin screwdriver, or allen-key/hex-wrench to push the edge of the bearings up from the bottom of the idler housing.

11b. However, if you plan to replace the bearings then it is safe to remove the rod from the bearings first, and then push the bearings out from the top of the idler.

12. If the bearings are being replaced then mark along the length of one bearing where one of the lines of metal ball-bearings are inside the bearing set, and mark a line on the other between two lines of bearings. (This ensures that the two sets of bearings can be aligned to touch on separate parts of the smooth steel rod).

13. If the bearings are being replaced then put the new bearings on the smooth Z rod, being careful to slide the rod in straight, so as to not push out any of the tiny ball bearings

14. Push the bearing sets into the new X-carriage idler, being sure to align the marks on the bearings with the channel in the idler part. Ensure that the first bearing set is pushed right to the bottom of the channel, touching against the lip. Ensure the second bearing set is pushed so that it is flush with (but not protruding from) the top of the idler part.

15. Put the two captive nuts, used to secure the T-nut inside the new idler part, and secure the T-nut using the original screws. (this partially holds in the top linear bearing set)

16. Push the X-carriage idler part onto the end of the X rods, wriggling slightly to help it seat onto the rods. (Be careful not to let the Z rod slide out)

17. Ensure that the X belt is unhooked from the motor end, so that it is not under tension, and feed it into the channel in the X-carriage idler part.

18. Align the X-carriage idler pulley with the holes in the X-carriage idler part, ensuring that the belt is around it, and then secure using the original screw.

------------------------------------------------------------------------

19. Remove the motor from the X-carriage motor mount part. (loosen the 45 deg screw locking the left-most screw in place)

20. Remove the T-nut from the top of the X-carriage motor mount. (ensure that the captive nuts do not fall out - unlikely)

21. Remove the linear bearings from the X-axis motor end, similarly to the other side. If re-using the existing bearings then keep the bearings on the rod while removing. If you plan to replace the linear bearings then they rod can be removed, and then install the new bearings on the rod afterwards (making sure to mark the bearings, such that the lines of ball-bearings are at 45deg to each other between the two sets of bearings).

22. Slide the Extruder assembly towards the left side.

23. Remove the X-carriage motor mount part from the X-carriage rods.

24. Remove the captive nuts used to secure the T-nut to the motor mount (same steps as for the idler side)

25. Remove the 45 deg screw from the motor mount part, and remove the captive square nut from the back of the part. (you'll likely need lots of persistent knocking the part against a hard surface to shake it out, and maybe a small jewelly screwdriver, or other fine-tipped implement to ease it out)

26. Insert that captive square nut into the new part, and partly thread the 45deg screw, just enough to hold the captive nut in place

27. Insert the linear bearings into the X-carriage, making sure to use the markings to align in the part, such that the lines are ball-bearings are 45deg apart between the two bearing sets.

28. Push the X-counter motor-mount part onto the X rods (apply opposing force to the X idler part, and wriggle the motor mount until it seats fully).

29. Feed the X belt through the slot in the motor mount, also ensuring that the belt is around the pulley on the idler end

30. Re-attach the X motor, first using the bottom-right screw, ensuring that the belt is around the motor gear, and then the top-left screw, followed by the top-right screw. At this point the screws should be left loose so that they are only just 'bite'.

31. Tighten the 45 degree tensioner screw to tighten the belt, just enough so that the belt is tight, and springs back to parallel when squeezed together, but so that the top-left screw can still be tightened.

32. Tighten all of the motor-mount screws.

**Installing new Z mounts**

1. Install the new and improved Z-axis motor mounts on the frame using the original screws (both sides)

2. Push each of the smooth Z-rods into the hole in the Z motor mounts (to avoid pushing it through too far, you can hold something up against the underside of the motor mount, where the motor would normally sit)

3. Install the new Z-axis top stoppers, using the original screws, ensuring that the top of the Z axis rods are properly located in the holes for them.

4. Slide the X-carriage to the top of the Z motion

5. Install each Z motor, by threading the screw rod into the T-nuts on the X-carriage, and sliding the motor assembly into the motor mount.

6. Ensure that the tops of the screw rods sit into the recess in the Z top parts

6. Secure each motor (loosely) using the rear two screws

7. Insert the front pieces into each of the motor mounts

8. Insert the front screws into each of the motor mounts, and tighten all 4 screws securing the Z motors.

9. Replace cable-ties securing the Z-motor wiring

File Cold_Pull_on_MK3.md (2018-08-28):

For best results, do your cold pull with some cleaning filament. eSun makes some that works well. These instructions assume you are using cleaning filament.

Using the Settings/Temperature menu, bring the Nozzle temperature up to the temperature you would extrude whatever filament you *were* using.

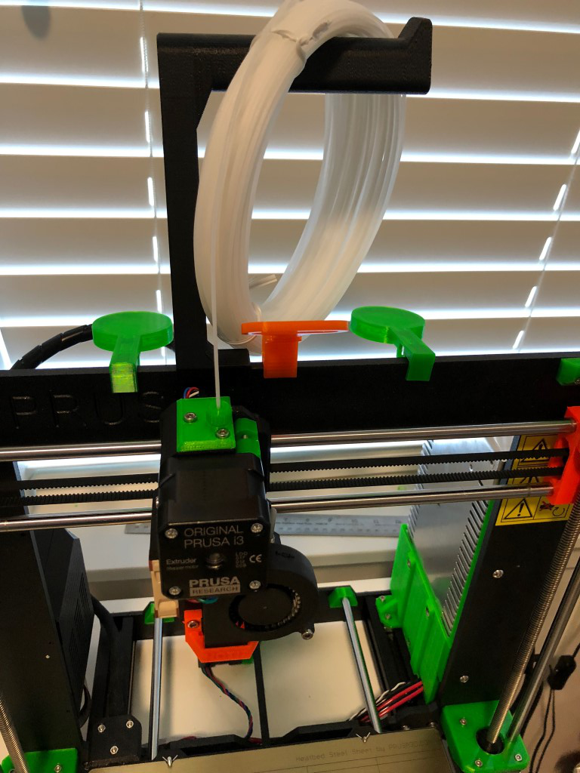
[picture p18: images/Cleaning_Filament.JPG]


Load the cleaning filament in the extruder. I like to answer “No” (once) when prompted if it is extruding the correct color, so that I flush a good amount of the cleaning filament through.

Go back in the Settings/Temperature menu, and set the temperature to zero (alternatively - Preheat / Cooldown).

Go find something to do while the nozzle cools down. I usually let it go until the fan turns off (around 40C).

I like to open the idler door. Although optional, you're less likely to damage something if you do this, and if the filament jams on the way out, you'll have to do it anyway.

To open the idler door, first remove the little plug that blocks external light from getting into the filament sensor:

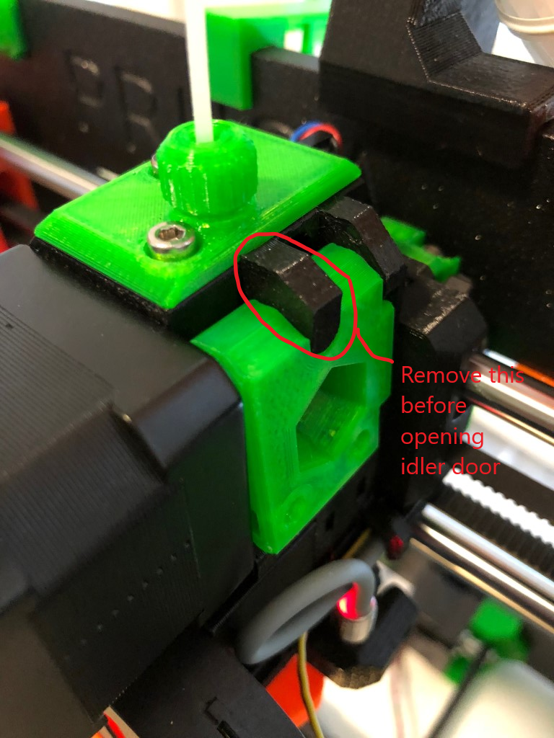
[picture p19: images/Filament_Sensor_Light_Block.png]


Next, you'll need to loosen the spring-loaded screws that hold the idler door closed:

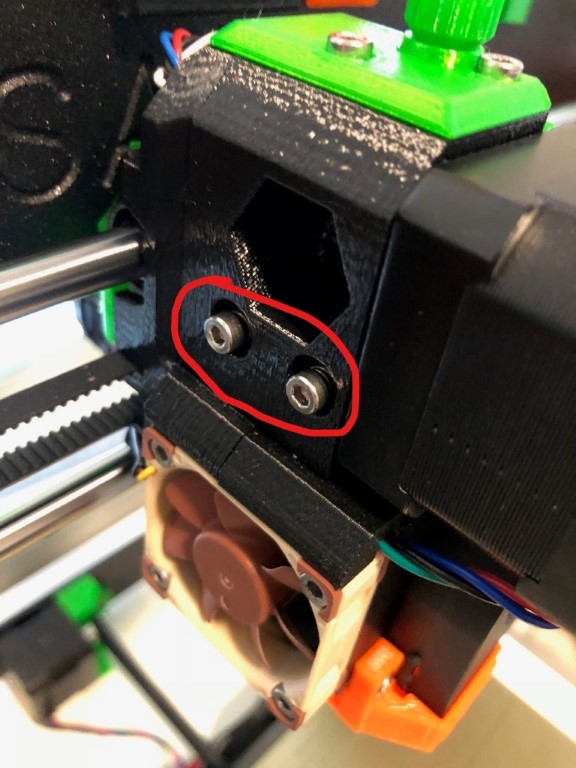
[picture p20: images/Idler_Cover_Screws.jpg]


Now swivel the idler cover door up. You should be able to see the filament inside.

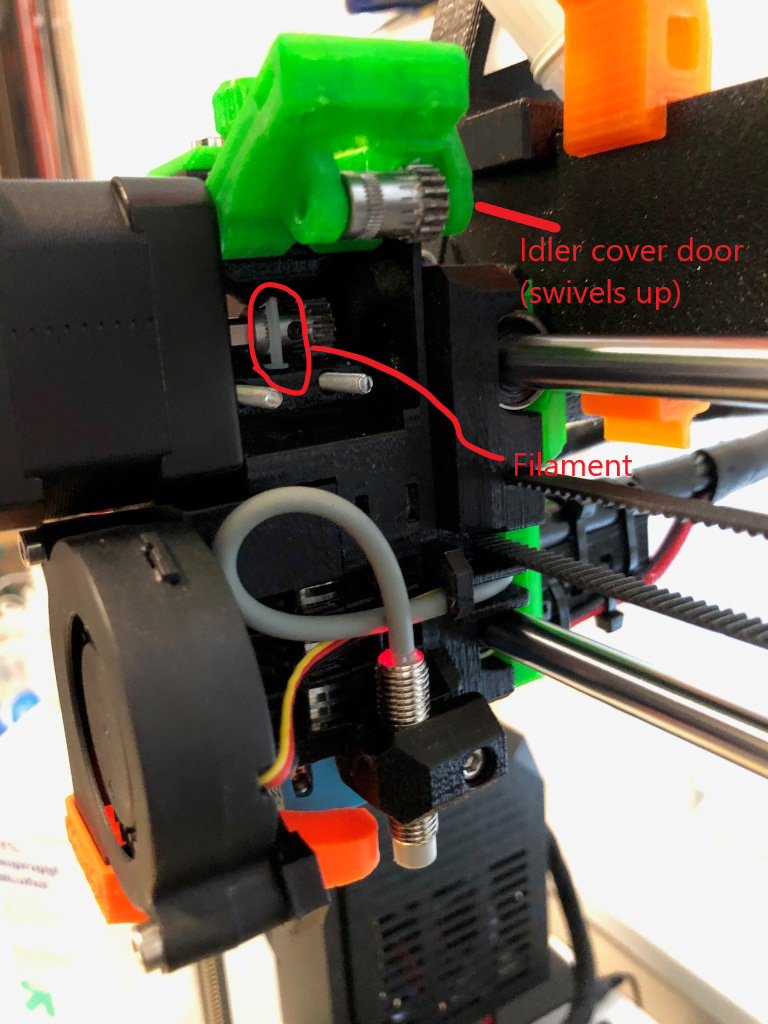
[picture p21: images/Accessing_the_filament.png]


Using the Settings/Temperature menu, set the nozzle temperature to 100C. Return to the top-level menu so you can monitor the temperature.

As the temperature passes 60C, the cleaning filament will start to soften. Grasp the filament near where it exits the extruder, and pull it with firm pressure. Don't use gorilla force - just enough to pull the filament out as it starts to melt. For me this usually happens around 80C. Due to a flaw in the Prusa designed E3D heat break, there is a good chance that the filament will get stuck. If it does, take some wire cutters and carefully cut the filament above the blob, so that you can pull it out the top. Then use pliers to pull out the piece that is still in the extruder. Examine the cleaning filament you just pulled out. Very often you will see a bit of colored filament embedded in this. This is residue from filament you were using.

If you choose (I don't), repeat the process (step 1 - 7) to make sure the nozzle is really clean.

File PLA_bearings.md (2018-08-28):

PLA bearings are just a great idea. (Needs Verification)

They are cheap, printable, lightweight, silent, accurate and they CAN work flawlessly.

This is what I use <https://www.thingiverse.com/thing:2202854> but there are other designs. I recommend reading through the attached texts on Thingiverse too.

Preparing the STL
-----------------

You need to download the [OpenSCAD](http://www.openscad.org) file from Thingiverse. Then fill up some parameters you want your bearings to have. There are some suggested values in the comments too. Don't fiddle with this too much for the first iteration, you need something to start with. Remember to fill up proper extrusion width that you use in your slicer. I also use 8 teeth on most of my bearings.

Slicing and printing
--------------------

You need to ensure there is no infill / gaps filing. This should be printed used only perimeters, see the attached images on Thingiverse. Set the number of perimeters in slicer according to value in the OpenSCAD file. I print mine with 0.4mm nozzle on 0.2 layer height. Also, ensure that the seam is set to aligned, so you can sand it off later easily or align the bearing so it does not cause problems. Always put at least two of them on the plate a bit far from each other, otherwise, they may have not enough cooling and your results will be different when you put more on the plate later. When you are iterating to find proper sizing, you can always stop the print midway and try them, so you save some time and filament. Then print those.

Post processing
---------------

You need to take the rods off your printer, degrease them (I use soap and water). Try pushing the bearing on the cleaned rods, top layer first (the bottom might get squished during print). They should be mildly hard to get there, but nothing like you need a hammer to do it. It also should not be too easy. If they are too small or large, change the inner diameter in OpenSCAD, slice, and print again. TODO: video of the right ID crude bearing

After you got the right tightness of the crude bearings, you should slide them up and down very quickly on the rods, until the rod gets pretty hot. Try to move things parallel and not to twist the bearing, as this may introduce clearance issues. If you do this right, you will feel that the bearing has less and less friction. When the friction does not improve anymore, it is time to stop. Do not remove the bearing from the rod. Let it cool down and try sliding it. There should be NO sticking to the rod, it should move freely, if you hold the bearing (do not hold it too tight), the rod should slide through it freely on its own weight. If you slowly slide the bearing on the rods using finger, there should be NO 'unsticking' happening. If it does, you need to process the bearing a little bit more. If there is clearance to the bearing, and it does wiggle on the rods significantly, you need less post processing or something fishy happened to the print. TODO: video of the desired behavior

Installing the bearings
-----------------------

These bearings are plastic. That means, you should not tighten them somewhere using screws, otherwise they WILL deform. Your best chances are using the classic linear bearing housing. Worst case use zip ties. This does make these almost useless on the mk3 (u-screws, X backplate...) unless you encase them in a metal casing.

You can use the crappy lm8uu bearings, pull the guts out of them, and find the right OD to make inserts like I did.

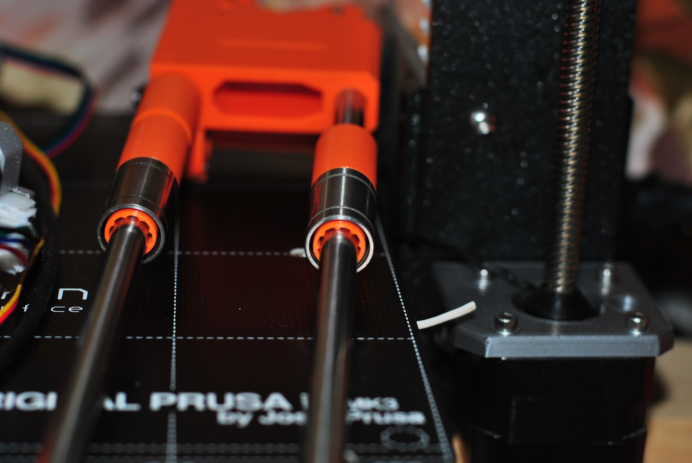
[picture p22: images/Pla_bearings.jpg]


Or you can find some steel pipe with the right outer diameter (15mm for LM8UUs), get it cut on the desired length and make proper fitting inserts for the pipe. This is the most ideal solution in my opinion.

They are still very sensitive to overtightening even in the lm8uu metal casing, so do not overtighten.

F.A.Q.
------

### How fast do they wear off?

When using proper lubrication, they can last for a very long time. I've had them installed on my previous printer for 400+ print hours, and they are like new, without any signs of wear.

### What is proper lubrication?

I use lithium grease and it works well. Do not use oil-based lubricant as this might end up in a gooey mess.

### Can you just provide me STL / gcode?

I can, but it is useless. You need to find proper sizing in 1/100s of a millimeter which would vary when using a different printer, or filament, or settings, or rods. You need to edit them in OpenSCAD on your own until you find the proper fit.

### Do they stick to rods and introduce backlash to axes?

When properly post-processed, they do not stick to the rods.

### Are they silent?

Yes. They are very silent. <https://drive.google.com/open?id=1dRCuqLUuqVaeE8ck3g-9f8ysJidY7OxA>

### Will they fail in a heated chamber?

Depends on the amount of heat. I printed ABS in heated cardboard chamber with these installed and I had no problems. The rods themselves probably provided enough cooling to those. Your mileage may vary though. It may be a good idea to use HTPLA if you plan on printing in a heated chamber.

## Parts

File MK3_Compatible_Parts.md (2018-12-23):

This page lists sources and part numbers for various replacement parts for the Original Prusa i3 MK3 printer.

Electrical Components
---------------------

### Connectors

| Part Name | Used In / Description | Manufacturer Part Number | Source / Source Part Number |
|---|---|---|---|
| 4-pin connector (body) | Keyed, 4-pin connector used on Einsy for connections to stepper motors. | Molex: 50-57-9404 | [Mouser: 538-50-57-9404](https://www.mouser.com/ProductDetail/Molex/50-57-9404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)<br/>[Digikey: WM2902-ND](https://www.digikey.com/products/en?keywords=50-57-9404)<br/>[TME: MX-70066-0178](https://www.tme.eu/en/details/mx-70066-0178/raster-signal-connectors-254mm/molex/050579404-50-57-9404-70066-0178/) |
| 3-pin connector (body) | Keyed, 3-pin connector used on Einsy for connection to fan. | Molex: 50-57-9403 | [Mouser: 538-50-57-9403](https://www.mouser.com/ProductDetail/Molex/50-57-9403?qs=%2fha2pyFaduiPWr18IEorNqpPP4cjWNMViqfOMj10Fc4%3d)<br/>[Digikey: WM2901-ND](https://www.digikey.com/products/en?keywords=50-57-9403)<br/>[TME: MX-70066-0177](https://www.tme.eu/en/details/mx-70066-0177/raster-signal-connectors-254mm/molex/050579403-50-57-9403-70066-0177/) |
| 2- pin connector (body) | Keyed, 2-pin connector used on Einsy for connections to thermistors and the Power Panic board. | Molex: 50-57-9402 | [Mouser: 538-50-57-9402](https://nl.mouser.com/ProductDetail/Molex/50-57-9402?qs=%2fha2pyFaduiPWr18IEorNpBHxdeTKRCsjuzRjqU7ETU%3d)<br/>[DigiKey: WM2900-ND](https://www.digikey.com/products/en?keywords=50-57-9402)<br/>[TME: MX-70066-0176](https://www.tme.eu/en/details/mx-70066-0176/raster-signal-connectors-254mm/molex/050579402-50-57-9402-70066-0176/) |
| Terminal / Pin for keyed connectors | Female terminals (pins) used in 4-pin and 3-pin keyed connectors on the Einsy board. | Molex: 16-02-0097 | [Mouser: 538-16-02-0097](https://www.mouser.com/ProductDetail/Molex/16-02-0097?qs=sGAEpiMZZMtVoztFdqDXO%252bpSlI4T0Hse)<br/>[DigiKey: WM2513-ND](https://www.digikey.com/products/en?keywords=16-02-0097)<br/>[TME: MX-16-02-0097](https://www.tme.eu/en/details/mx-16-02-0097/raster-signal-connectors-254mm/molex/016020097-70058-0206/) |

### Motors

| Part Name | Used In / Description | Manufacture Part Number | Source / Source Part Number |
|---|---|---|---|
| X,Y,E stepper motor | X, Y, E axis | -  [LDO XYE motor drawing](https://github.com/PrusaOwners/prusa_docs/blob/master/mk3_parts/LDO-42STH38-1004A100CM-RevA-for-3D.pdf)<br>-  [LDO XYE motor specs](https://github.com/PrusaOwners/prusa_docs/blob/master/mk3_parts/LDO_XYE_complete_datasheet.ods) | LDO-42STH38-1004A100CM-RevA-for-3D |
| Z stepper motor | Z axis | - [LDO Z motor drawing](https://github.com/PrusaOwners/prusa_docs/blob/master/mk3_parts/LDO-42STH34-1004L321E100CM-RevA-for-3D.pdf)<br>- [LDO Z motor specs](https://github.com/PrusaOwners/prusa_docs/blob/master/mk3_parts/LDO_Z_complete_datasheet.ods) | LDO-42STH34-1004L321E100CM-RevA-for-3D |

### Fans and Blowers

| Part Name | Used In / Description | Specification | Manufacture Part Number | Source / Source Part Number |
|---|---|---|---|---|
| Noctua fan | Hotend fan | - 5V<br>- 0.05A<br>- 4500 RPM<br>- Size: 40x40x10 mm<br>- Mounting hole spacing: 32x32 mm<br>- Airflow: 8,2 m³/h (4.83 CFM)<br>- Static Pressure: 1,78 mm H₂O | Noctua NF-A4x10 5V | [Noctua website](https://noctua.at/en/products/fan/nf-a4x10-flx) |
| 5015 Blower fan | Nozzle fan | - 5V<br>- 0.30A<br>- 4500 RPM<br>- Size: 50x50x15 mm<br>- Mounting hole spacing: 38x43 mm<br>- Airflow: 3.8 CFM | ? | ? |

### Heated Bed

| Part Name | Used In / Description | Specification | Manufacture Part Number | Source / Source Part Number |
|---|---|---|---|---|
| Magnets | Magnets for MK52 heated bed | - Neodymium Material Type: N35UH<br>- Size: 20x6x2.3 mm<br>- Hole depth in MK52: 2.5-2.7 mm<br>- Maximum Operating Temp: 180°C | ? | ? |

### Cable Management

| Part Name | Used In / Description | Specification | Manufacturer Part Number | Source / Source Part Number |
|---|---|---|---|---|
| Wrap Braided Cable Sleeve | MK52 Heated bed and X-axis stepper | - Material: Polyester<br>- Diameter: 5mm<br>- Length: 300mm | HellermannTyton: 170-01000  | [Conrad: 541298](https://www.conrad.com/ce/en/product/541298/HellermannTyton-170-01000-Twist-In-05-Helagaine-Meshwork-Hose-Black) <br/> [AliExpress: Clone](https://www.aliexpress.com/item/Black-Wrap-Braided-Cable-Sleeve-5mm-3m-General-Wire-Pipe-Hose-Indoor-Wiring-Protection-Flexible-Nylon/32839976444.html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) |
| Wrap Braided Cable Sleeve | Hotend assembly cable bundle | - Material: Polyester<br>- Diameter: 13mm<br>- Length: ? | HellernammTyton: 170-01002  | [Conrad: 540704](https://www.conrad.com/ce/en/product/540704/HellermannTyton-170-01002-Twist-In-13-Helagaine-Meshwork-Hose-Black) |
| 3mm nylon cable | Support for extruder cables | - Material: Nylon<br>- Diameter: 3mm (not 2.85mm like nylon filament!)<br>- Length: ? | ? | ? |

### Power Supply

| Part Name | Used In / Description | Specification | Manufacturer Part Number | Source / Source Part Number |
|---|---|---|---|---|
| Delta PSU 24V 320W | Compatible PSU for MK3 | 24V 320W | Delta PMF-24V320WCAB | [Delta website](http://www.deltapsu.com/products/panel-mount-power-supply/PMF-24V320WCGB) |
| Mean Well PSU 24V 320W | Compatible PSU for MK3| 24V 320W | Mean Well SP-320-24 | [Mean Well website](https://www.meanwell.com/webapp/product/search.aspx?prod=SP-320) |

### Power Cables and Connectors

Always get known brand from reliable source for those parts, they are critical and might be dangerous if not correctly manufactured.

| Part Name | Used In / Description | Specification | Manufacturer Part Number | Source / Source Part Number |
|---|---|---|---|---|
| 115/230 VAC Cables | PSU | 16 AWG or 1.5mm<sup>2</sup> | | | |
| 12/24 VDC Cables | PSU to Rambo/Einsy | 14 AWG or 2mm<sup>2</sup> | | | |
| Terminal Quick Connects Connector | Power plug, Power switch | - 16 AWG<br>- Tab width: 6.35mm (according to your power plug and switch connectors)<br>- Fully insulated | | [Digikey](https://www.digikey.com/products/en/connectors-interconnects/terminals-quick-connects-quick-disconnect-connectors/392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) |
| Terminal Spade Connector 115/230 VAC | PSU (115/230 VAC) | - 16 AWG<br>- Flanged terminal type<br>- #6 Stud/Tab size<br>- Insulated<br>- Spade width: 6.35 to 8mm | | [Digikey](https://www.digikey.com/products/en/connectors-interconnects/terminals-spade-connectors/391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) |
| Terminal Spade Connector 12/24 VDC | PSU (12/24 VDC), Rambo/Einsy | - 14 AWG<br>- Flanged terminal type<br>- #6 Stud/Tab size<br>- Insulated<br>- Spade width: 6.35 to 8mm | | [Digikey](https://www.digikey.com/products/en/connectors-interconnects/terminals-spade-connectors/391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) |
| Terminal Ring Connector | Heated bed | - 14 AWG<br>- M3 Stud/Tab size<br>- Insulated<br>- Spade width: 6.35 to 8mm | | [Digikey](https://www.digikey.com/products/en/connectors-interconnects/terminals-ring-connectors/394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) |

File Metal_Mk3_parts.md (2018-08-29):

There are metal replacement parts for many of the traditionally PETG 3D printed parts for the Mk3 available online.

We are not yet aware of anyone who has done an objective test of these (measuring tolerance vs spec, measuring flex or vibration etc), so these are not yet recommended.

However links to these parts are below: -

[Aluminum Y-axis rod holder/clamp](https://www.aliexpress.com/item/4pcs-Prusa-i3-MK3-Y-axis-smooth-rod-holder-clamps-black-anodized-aluminum-rod-front-rear/32861668476.html)

[Aluminum Y-axis belt holder](https://www.aliexpress.com/item/1pcs-Prusa-i3-MK3-black-anodized-aluminum-alloy-Y-Belt-Holder-for-Reprap-Prusa-i3-MK3/32876552268.html)

[Aluminum Y-axis motor mount and idler end](https://www.aliexpress.com/item/aluminum-alloy-Prusa-i3-MK3-3d-printer-Y-end-motor-holder-and-Y-end-idler-kit/32879217205.html)

[Aluminum X-axis motor and idler ends](https://www.aliexpress.com/item/-/32879096023.html)

[Aluminum Z-axis mounts](https://www.aliexpress.com/item/1set-Prusa-i3-solid-fixed-Z-axis-mounts-kit-with-8mm-bearing-for-TR8-lead-screw/32854324917.html)

-&gt; I would not recommend those Z tops with bearings. the lead screw should not be constrained, only the smooth rod.

Note that for other brits out there, it's ok ... Aluminum is just how those American folks mis-spell Aluminium :)

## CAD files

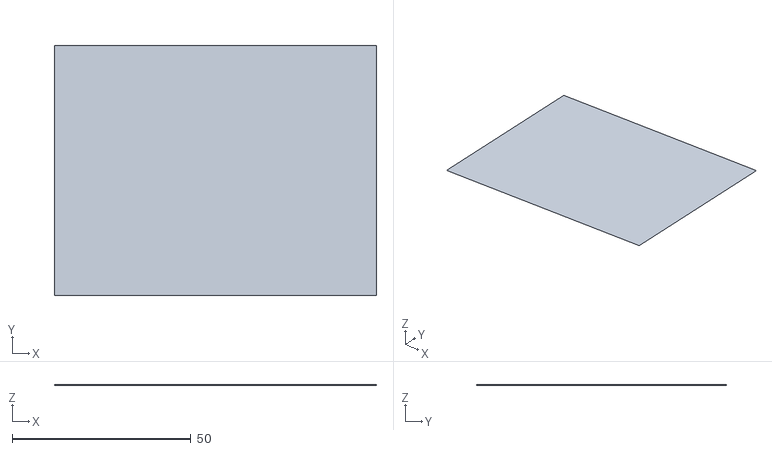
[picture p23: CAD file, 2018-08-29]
files/1st_layer_35C.stl
90.0 x 70.0 x 0.2

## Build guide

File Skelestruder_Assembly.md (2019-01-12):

### Note: these are deprecated.  Please see [Dozuki instructions](https://www.ifixit.com/Device/Skelestruder_for_Prusa_MK3)

SPV1 (b3.1)
===========

HW (vitamins)
-------------

What parts you need to acquire, including some you can harvest from spares or the stock extruder.

| Parts | For Stock | For Skelestruder  | Notes |
|---|---|---|---|
| **Required** | | | |
| Filament sensor | 1 | 1 | Stock MK3 Filament Sensor |
| Bowden | 1 | 1 | For filament inlet |
| E3d extruder assembler | 1 | 1 | |
| Bondtech drive | 1 | 1 | Standard Bondtech Drive Gear |
| Bondtech idler with bearings | 1 | 1 | |
| BondTech axle | 1 | 1 | |
| PTFE x 13mm | 1 | 1 | |
| Nylon washer | 2 | 2 | |
| Spring | 2 | 1 | |
| M3x10mm screw | 10 | 9 | For M3 hardware, check your local hobby shop first, or order from [Bolt Depot](https://www.boltdepot.com/Metric_socket_cap_Stainless_steel_18-8_(A-2)_3mm_x_0.5mm.aspx) |
| M3x30mm screw | 4 | 1 | |
| M3x40mm screw | 4 | 2 | |
| M3x18mm screw | 7 | 3 | |
| M3 sq nut | 11 | 4 | |
| M3 hex nut | 4 | 6 | Spares (if MK3 bought as kit, otherwise purchase) |
| M3x25mm screw | 2 | 3| Spares |
| Zip ties | 0 | 2| Spares (if MK3 bought as kit, otherwise purchase) |
| M3 Nylock nut | 0 | 2| Spares (if MK3 bought as kit, otherwise purchase) |
| M3x20mm screw | 0 | 1| Spares? (if MK3 bought as kit, otherwise purchase) |
| M3x6mm screw (or 4, or 8) | 0 | 1 | Purchase |
| M3x12mm screw | 0 | 2 | Purchase |
| 105zz bearings | 0 | 3 | [Purchase](https://www.amazon.com/gp/product/B00ZHSTKCE) |
| 140x6mm GT2 loop belt (70 teeth) | 0 | 1 | [Purchase](https://www.robotdigg.com/product/88) |
| 5x45mm Shaft (Longer is OK) | 0 | 1 | Purchase<br />Easiest USA: [Custom order with flats](https://us.misumi-ec.com/vona2/detail/110302634310/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)<br />Easiest UK: [Custom order with flats](https://uk.misumi-ec.com/vona2/detail/110302634310/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)<br />(double check 3D render to make sure you see two flats)<br />Lightest: [requires some prep (see below)](https://www.amainhobbies.com/sab-steel-5mm-tail-spindle-shaft-sabh0329-s/p275071)<br />Cheapest: [100mm raw shaft](https://www.amazon.com/uxcell-100mm-Model-Straight-Metal/dp/B01B27MJC6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) | Longer is ok  <br> Available pre-cut with current flat from Misumi  <br> UK source: https://uk.misumi-ec.com/vona2/detail/110302634310/?HissuCode=SSFJ5-45-WFC4-A13-E6 |
| **Optional, but recommended** | | | |
| Short body Nema17 stepper motor  | 0 | 1 | The stock motor can be used, but a slimline motor will help reduce the weight of the extruder. <br /> I recommend getting one with wire plug on motor for easier assembly.<br />Nema14 is also supported, but Nema17 provides more torque and better center of mass.<br /> **Motor purchase** [US](https://www.amazon.com/Short-Bipolar-Motor-18-4oz-13Ncm/dp/B00PNEQ79Q), [UK E3D](https://e3d-online.com/nema17-slimline-stepper-motor). <br />The plug on the Einsy side of the cable can be purchased from [Ultimachine US](https://ultimachine.com/products/2-54mm-1x4-connector-positive-latch-housing-kit-5-pack),  [RS UK](https://uk.rs-online.com/web/p/products/6783161) (and crimp terminals [RS UK](https://uk.rs-online.com/web/p/pcb-connector-contacts/6794745/)).|
| New PTFE tubing | 0 | 1 | [Purchase: Filastrude US](https://www.filastruder.com/collections/e3d-spare-parts-and-accessories/products/capricorn-ptfe-tubing) <br />[Purchase: E3D UK](https://e3d-online.com/capricorn-bowden-tubing) |
| New GT2 belt to replace X belt.  | 1 | 1 | New X belt is shorter than stock due to new carriage connection. Can just trim stock one instead. |
| Cleaning brush wheel | 0 | 1 | [Purchase](https://widgetsupply.com/product/ban14.html) |
| **Optional** | | | |
| 14T pulley | 0 | 1 |(only for 4:1)<br />[Purchase](https://openbuildspartstore.com/gt2-2m-timing-pulley-14-tooth/) |
| 20mm unmount wheel brush | 0 | 1 | Used for gear cleaner.<br />[Purchase](https://widgetsupply.com/product/ban14.html) |
| 673 (MR63) bearing | 0 | 1 | Used for indirect sensor<br />[Purchase](https://www.amazon.com/gp/product/B00ZHSQX42/ref=oh_aui_detailpage_o00_s00?ie=UTF8&psc=1) |
| M5 heat set nut | 0 | 1 | For MMU2 (https://www.amazon.com/gp/product/B077CG1W3L/ref=oh_aui_detailpage_o01_s00?ie=UTF8&psc=1) |

Note: Source links for purchase in table above are for reference only. Other suppliers are available depending on your level of impatience :-)

Printed Parts
-------------

**Important**: before you start printing parts, please calibrate your extrusion using this tester: <https://www.thingiverse.com/thing:2996626>

Most of the parts of the skelestruder are 3D printed. One of the nice features of skelestruder, is there are considerable options, in terms of colors and material choices, for these printed parts, allowing you to customize the look and feel. However, there are some basic ground rules you should adhere to in order to not run into issues. In the table below, we will list all the parts, the options for printing each, and notes about how they should be printed. By reading through this table, please be aware of the following:

-   You only need one variant for parts shown with multiple.
-   There are a couple of tools that are optional to print, but will help you with assembly.
-   I exclusively tested with Slic3r. Other slicers should work but your mileage may vary.
-   Parts are designed to fit with high precision. If you deviate from the print settings too much, you may run into problems when you try to assemble.

### Filament Choice

The material recommendations in the printed parts table are based on a mix of experience, expectations, strength, density, glass temp, etc. You can deviate. Let me know what you find. Remember, I am going for light so I want good stiffness/density. For example, motor spider needs to be stiff so I recommend PLA since it has a much higher modulus of elasticity. Here’s a table where I ranked various properties. Note that HT PLA needs to be annealed and it can shrink/distort during that process if you are not careful, leading to fitment issues.

| Material | Weight | Stiffness | Stiffness / Weight | Deflection Temperature | Detail Resolve | Environmental Friendliness | Post-processing | Ease of Printing |
|---|---|---|---|---|---|---|---|---|
| PLA (HT) | B | A | A | C (A) | A | A | A | A |
| PETG | B | C | C+ | B | B | F | C | B+ |
| ABS | A- | C | B- | A | D | F | A | C |
| Nylon | A | F | F | A- | B | F | ? | D |
| PETG-CF | B | A+ | A- | A+ | A- | F | ? | A- |
| Nylon-CF | A- | A+ | A+ | A+ | A- | F | ? | A- |
||

Anecdotally, I have been testing all parts 100% PLA because I have a bunch of spools to burn through. I have had no problems. Others have also printed all parts in 100% PLA without any issues. Note that the extruder fan is blowing cool air over the lower portion the entire time, so very little is exposed to stagnant radiant heat, mainly the cooling nozzle and P rack. The cooling fan is on some even for PETG printing and P rack seems far enough away that I see no issues. I am not in an enclosure though.

Nylon is too flexible to be used for anything structural - it can be used for the fan nozzle but there is no real advantage to doing so.

Carbon fiber reinforced Nylon and PETG are both stiffer than PLA, have higher heat deflection temperatures than even ABS, and are incredibly low-warp and dimensionally stable.  Anecdotally, printing 100% in either of these gives the best results and noticeably reduces ghosting artifacts over PLA.  Highly recommended, just be aware of the effects of printing CF containing filaments on your nozzle first.

I design parts to minimize unique slicer settings, changing orientation, and post-processing. Ideally just print and go. That said, some post-print dressing is helpful. Before starting, clean up parts where they interface, such as removing burrs and blobs. Pre-tap threads in these holes by fully screwing and unscrewing a screw (will make assembly easier):

-   Shroud mounting holes
-   Cooler mounting hole
-   PINDA clamp (not rack)

Test fit all parts to make sure there are no obstructions:

-   Screws should slide through holes that aren’t tapped.
-   The shaft should fit into the wheel hub without too much resistance.
-   Alignment pins fit receiving holes.

It is better to know now and clean up or reprint as needed.

Loosen X motor and then disassemble and remove stock extruder and X carriage by reversing steps in Prusa instructions. Save all parts!

NOTE: pictures are for reference only, instead follow wording closely. Pictures may be from older builds with slightly modified parts.

### Parts Diagram

Refer to the following diagrams to identify the specific parts referenced in the instructions below.

<File:Skelestruder> Legend.jpg File:Skelestruder Legend.jpg

<File:Skelestruder> Legend Alt View.jpg File:Skelestruder Legend Alt View.jpg

### Parts List

| Part | Variant + File Name | PLA | HTPLA | PETG | Plate | Color | Notes |
|---|---|-----|---|---|---|---|---|
| E cage B | SP_Ecage_B_b3a.stl | | Y | Y | | User | Use 2 perimeters |
| E cage F | SP_Ecage_F17_b2b.stl | | Y | Y | | User | Remove one ring support |
| Spider | SP_spider14_b1.stl SP_spider17_b2.stl | Y | | | | User | |
| P rack | SP_Prack_b3a.stl | | Y | Y | | User | |
| S cartridge | SP_D_cartridge_b2b.stl SP_I_cartridge_b2b.stl SP_spring_b2.stl | Y | Y | Y | | Dark matte | |
| Inlet | SP_std_inlet_b1.stl SP_inlet_ptfe_b1.stl | Y | Y | Y | | User | Optionally print at 0.10 with 0.25 nozzle for tighter tolerances. |
| Cover | SP_cover_b2.stl SP_I-lid_b2b.stl | Y | | | | Dark matte | |
| Shroud | SP_shroud_b1.stl SP_shroud_b3.stl | Y | | | | User | |
| Knob | SP_knob_b2.stl | Y | | | | Visible | Can use Advanced / elephant foot = 0.25mm |
| Carriage | SP_carriage_b3.stl | Y | | | | User | Do not remove hooks |
| Key | SP_key_b3a.stl | Y | | | | User | |
| Xclamp | SP_X_clamp_b2b.stl | Y | | | | User | |
| Tail | SP_tail_b2.stl SP_fin_b1.stl | | | Y! | | User | PETG highly recommended, for flex on the fin |
| Idler | SP_idler_b2.stl | Y!  | | | Y | Visible | Plate |
| Wheel | SP_wheel_b2.stl | | | Y | | User | |
| Tread | SP_tread_b1.stl | Y!  | | | N | User | PLA highly recommended. Do NOT plate |
| Pinion | SP_pinion_b1.stl SP_pinion_deepflat_b2.stl | Y | | | N | User | 3 perimeters. Do NOT plate. Disable “detect thin walls”. |
| Spacer | SP_spacer_v1a4.stl | Y | | | Y | User | Plate |
| Bracket | SP_bracket_b1.stl SP_bracket_volcano_b2.stl | Y | | | Y | User | Plate |
| Cooler | SP_noz_v6_b3.stl SP_noz_volcano_b2.stl SP_noz_volcano_b3.stl SP_nozPR_a8.stl | | Y | Y | | User | |

Component/Part Prep
-------------------

Click on photos to enlarge

### Direct Cartridge

Insert filament sensor in cartridge. Screw down carefully, similar to PR instructions

-   1x M3x10mm

Insert smaller PTFE into cover inlet.

-   1x PTFE

Screw cover in corner onto cartridge a little bit for now

-   1x M3x10mm

Set aside safe

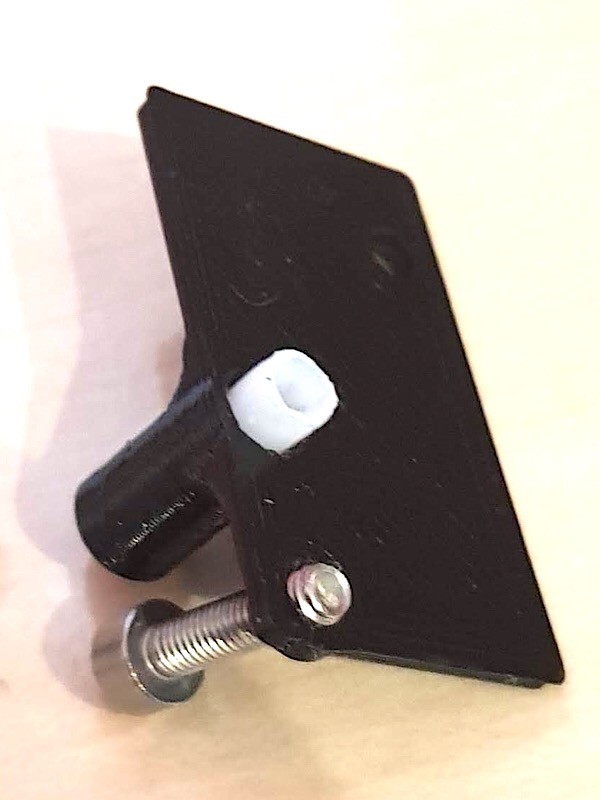
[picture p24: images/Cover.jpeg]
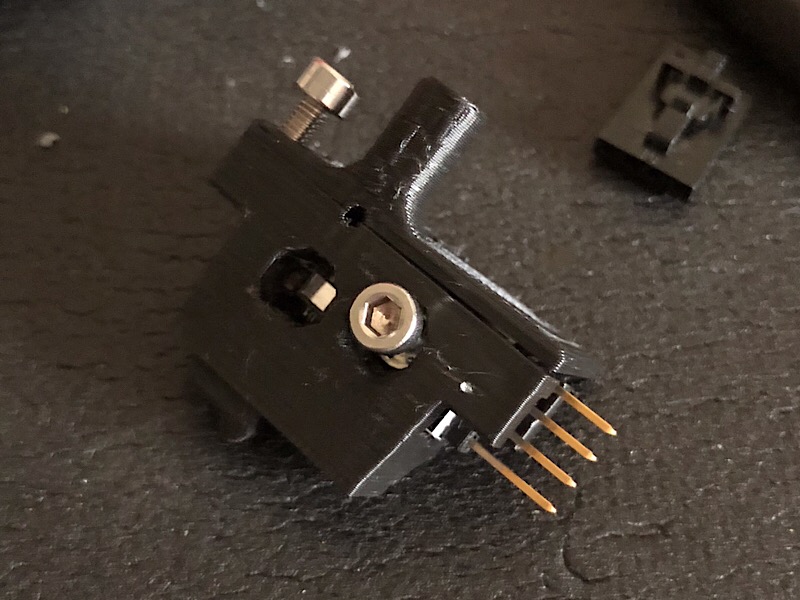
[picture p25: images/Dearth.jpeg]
 |PTFE in cover inlet  |Sensor cartridge

### Indirect Cartridge

Slip sensor in from end of I-lid and screw down

-   1x M3x10mm

Insert PTFE into I-lid inlet

-   1x PTFE

Slide 673 bearing onto spring about 1/3 (may need to chamfer ends with knife)

-   1x 673 bearing

Snap spring into I cartridge, then screw I-lid onto I cartridge and set aside

-   1x M3x10mm

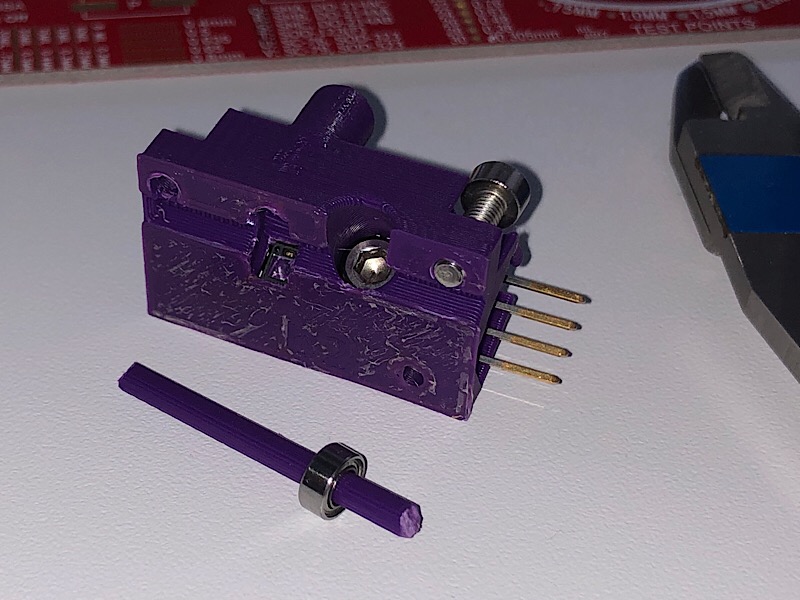
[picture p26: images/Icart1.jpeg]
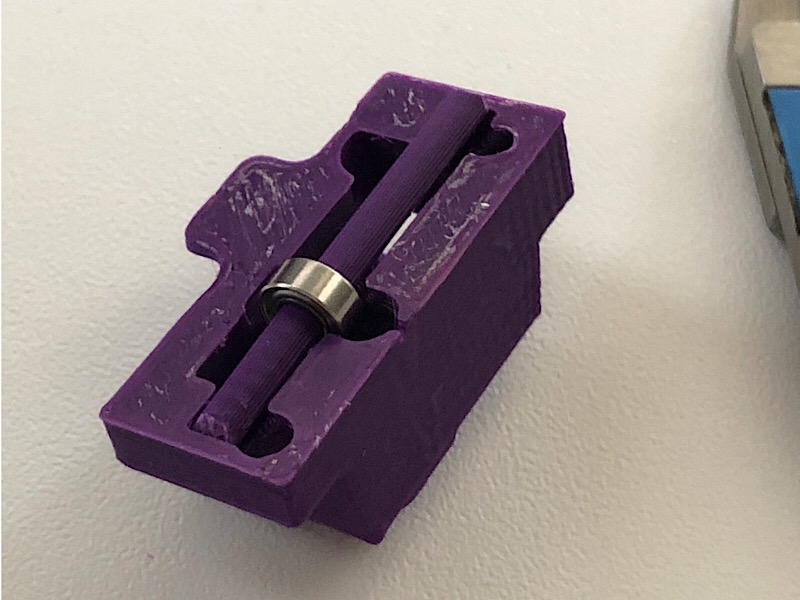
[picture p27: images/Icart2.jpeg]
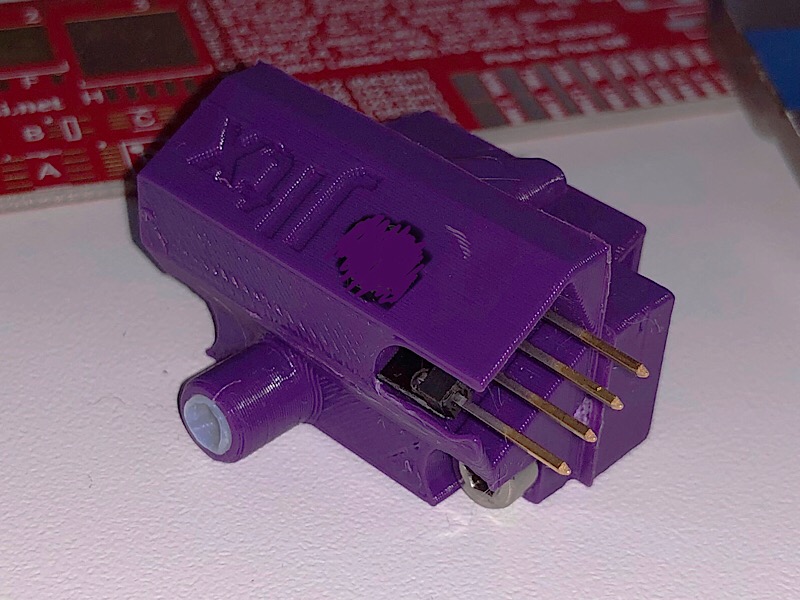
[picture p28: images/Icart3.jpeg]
|Start |Install |Done

### Carriage

Slip square nuts into slots in top bearing cups

-   2x sq nut

Make sure they are seated at bottom, can use 1.5mm hex wrench to press in. Use Sharpie to mark line on each bearing indicating ball line (needs to be done before assembling X gantry, otherwise don’t sweat it). Align bearings with bottom facing out, top two facing out but skew slightly (see picture) Snap carriage onto bearings. Zip tie top bearings, start from bottom hole and come out top hole (see 3rd pic)

-   2x zips

Snap x clamp onto bottom bearing. Screw down

-   2x M3x10mm

Insert two hex nuts into pockets on key block

-   2x hex nuts

Screw key onto front of carriage using hole below top bearings

-   1x M3x10mm

Screw tail or fin onto X clamp

-   1x M3x25mm

Do not attach belt yet. Slide carriage back and forth by hand to make sure it glides smoothly

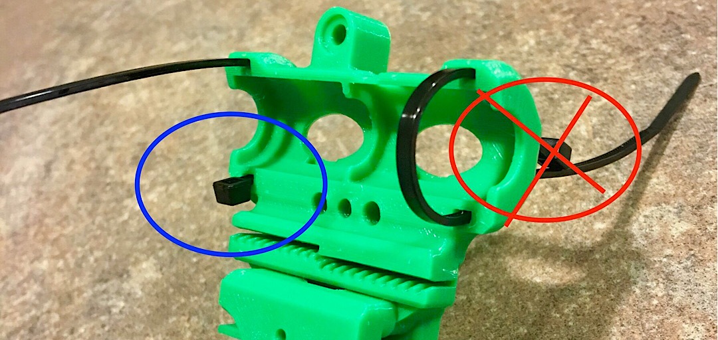
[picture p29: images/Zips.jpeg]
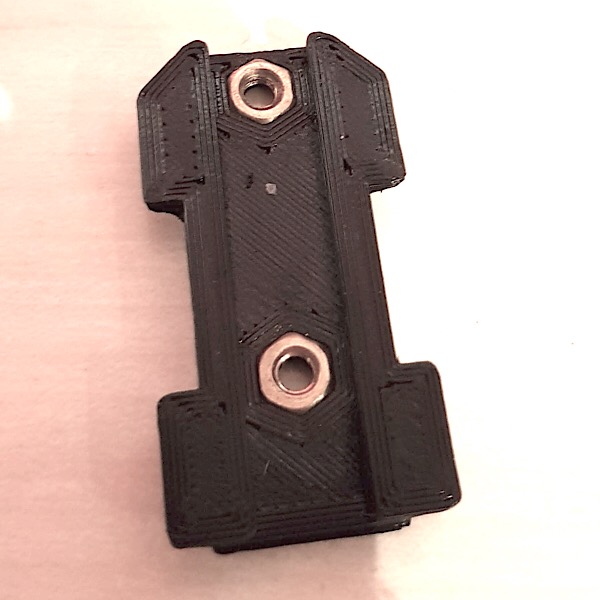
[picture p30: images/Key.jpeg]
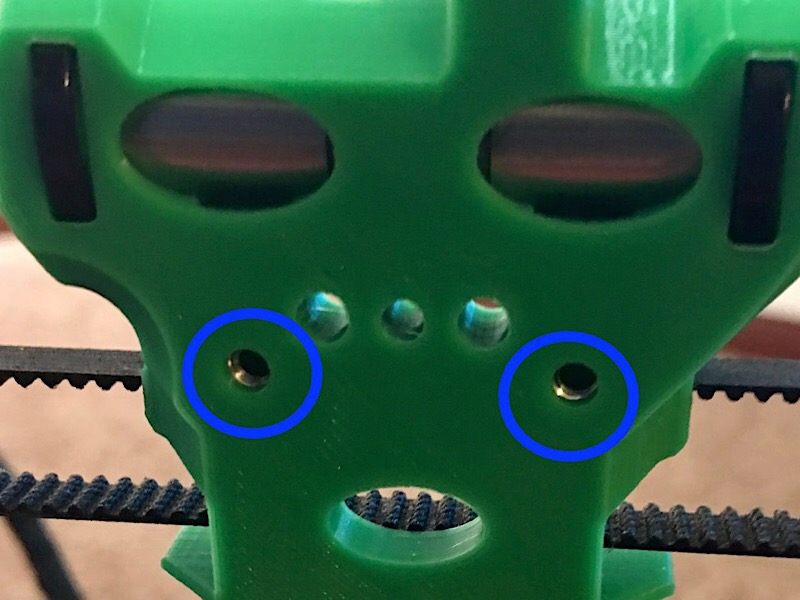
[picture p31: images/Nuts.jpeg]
  

### Inlet

If you want, you can swap out to Capricorn tubing which is more slippery. For ptfe inlet, trim ptfe tube to match inlet profile (see pic. Note that new inlet is now keyed unlike picture). *OR* for std inlet, straight cut flush to overall length of 38mm\[?? Need to confirm\]. If using new ptfe tubing, make sure bottom is both tapered and chamfered to match heatbreak -&gt; can use ptfe jig and razor blade. Push inlet onto Bowden of e3d

-   1x Bowden

### E-Cage

Insert Nyloc nut into top hole on cage F

-   1x Nyloc

Put one square nut into cage F at center, can use small screwdriver to help press in place

-   1x sq nuts

Press bearings into bearing holes on cage F & B so flush -&gt; can use bearing press if desired

-   2x 105 bearings

Slip motor anchor screw through bottom hole on cage F

-   1x M3x18mm

Insert to hex nuts in pockets on back of cage B

-   2x hex nuts (optionally can use nylock nuts)

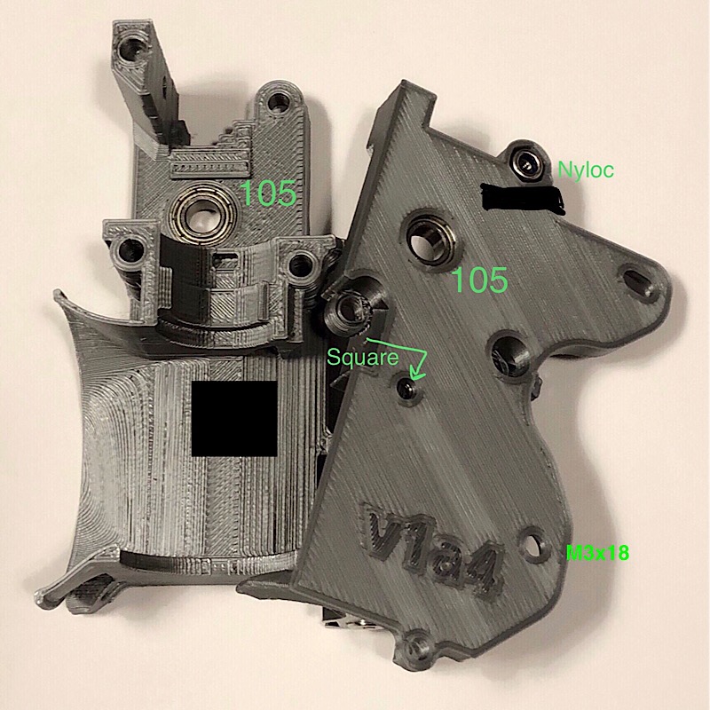
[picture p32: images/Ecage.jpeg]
 |Ecage

### P-Rack

Use free screw to make sure it slides through holes in knob holder braces. Can use threads to ream out slightly as needed. screw from bottom of P rack up until snug

-   1x M3x30mm

There is a hex nut pocket on top to lock screw, but I’ve found it does not slip without it Optional: you can thread cam (tab down) on top of P rack to remove any play once set insert hex nut into knob

-   1x hex nut

Slip knob between braces on cageB with nut facing \*down\* Note that there is one detent on knob that extends to edge which should be alined with tooth on brace to make it easier to insert carefully insert screw through bottom holder into knob and turn knob to start thread If using cam, make sure it is rotated back for clearance watch P rack to make sure it dovetails onto slide turn knob until P rack as approx as shown in photo

### E3d

Insert inlet and heatsink, aligning key, into E-Cage-B. Press E-Cage-F on top, first aligning top pin, then making sure inlet fits slot. Rotate heatsink so that heat block is straight. Also make sure Bowden aligned with inlet if tapered

Insert screws into middle

-   2x M3x25mm

Screw E-cage together using the two middle screws, snug but not tight. Slide long screw through top hole temporarily to make sure cage is aligned, then tighten down middle screws (not long screw!)

-   1x M3x40mm

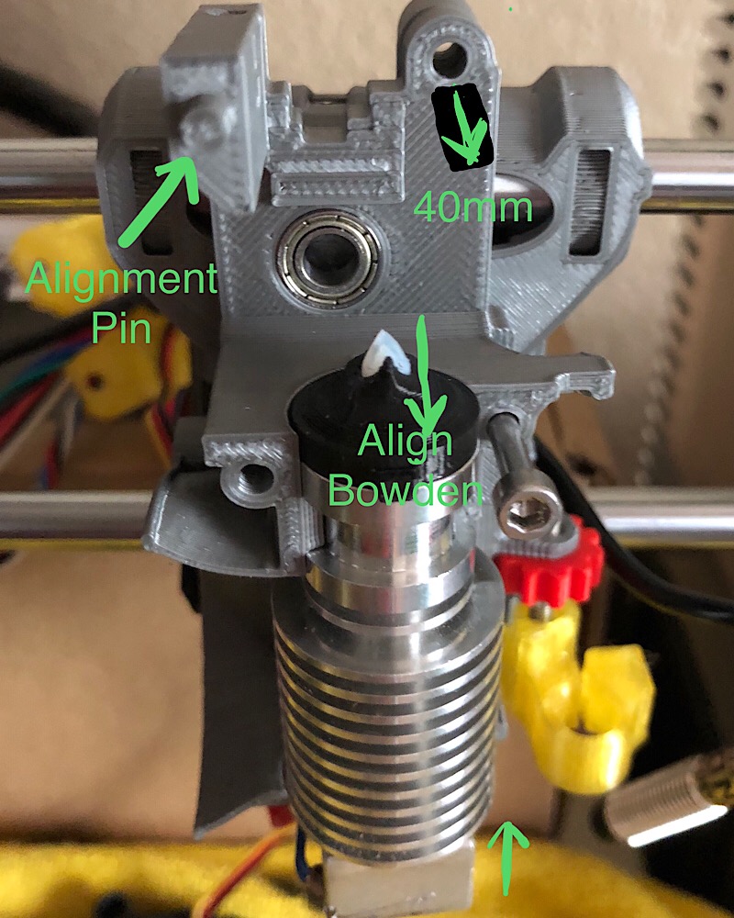
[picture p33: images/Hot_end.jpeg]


### Motor

Press bearing into spider hole so flush on both sides

-   1x 105 bearing

Press pinion gear onto motor shaft (keyed) with collar to outside (pic shows older metal pinion)

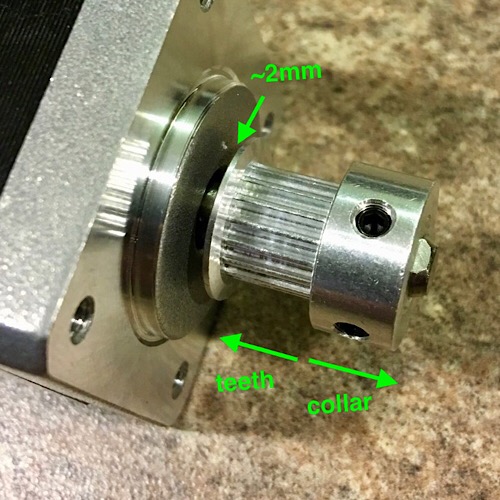
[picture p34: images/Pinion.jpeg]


### Noctua

Carefully screw shroud onto front edge of fan, it is delicate. Wires can go next to edge of top shroud, or away from shroud as shown in picture.

-   2x M3x18mm

Screws will stick through back of shroud, used for wire mgmt and hanging cooler later.

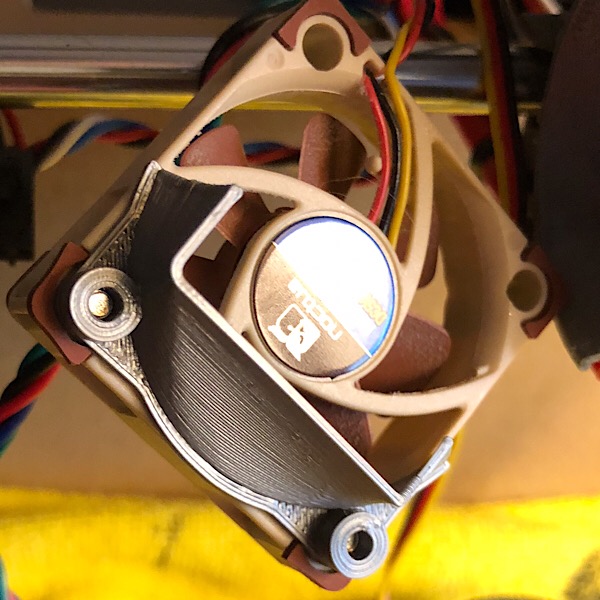
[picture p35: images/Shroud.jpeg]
|shroud

### Idler

With support cylinder still in place and flat side on table, press bondtech axle into idler until it hits cylinder (about 3mm)

-   1x axle

Note that one end of axle is slightly chamfered. This end should go in first. Now remove support cylinder by twisting with pliers add bond tech idler and bearings with teeth at bottom, press axle through.

-   1x bondtech idler w/ bearings

Counter-sink axle slightly to make sure axle bites both sides. Make sure gear spins freely

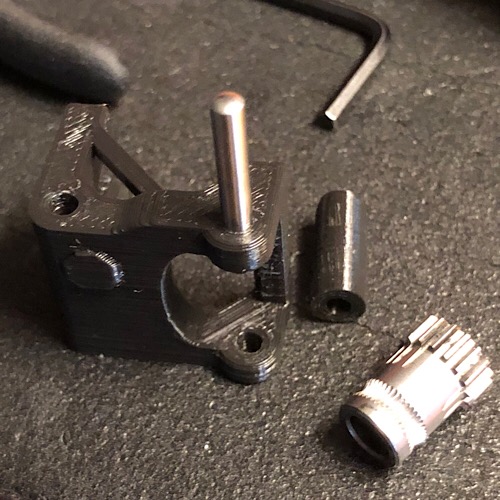
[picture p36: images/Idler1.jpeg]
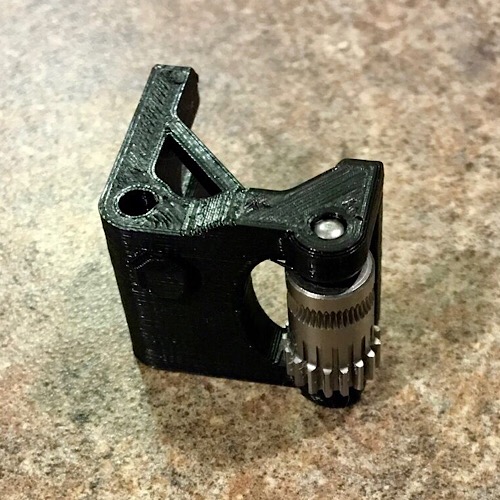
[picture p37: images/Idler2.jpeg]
 

### Tensioner

Insert hex nut into tensioner knob

-   1x hex nut
-   1x M3x40mm

Slide spring onto screw

-   1x spring

and lightly screw on tension knob so screw tip is flush with hex nut inside tensioner knob

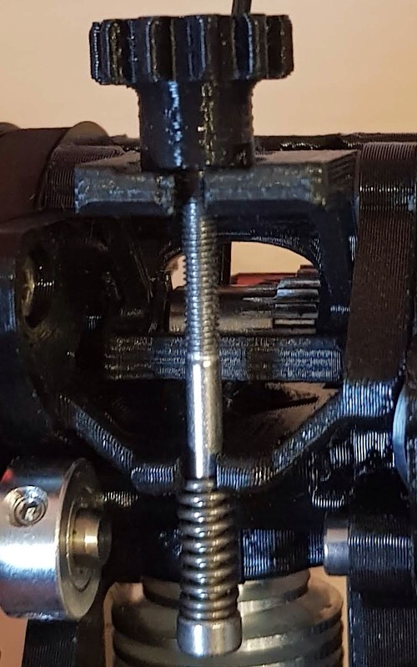
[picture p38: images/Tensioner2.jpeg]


### Part fan

Insert hex nut into bracket

-   1x hex nut or Nyloc (preferred)

screw onto top hole (near wires) of fan allowing rotation

-   1x M3x18mm

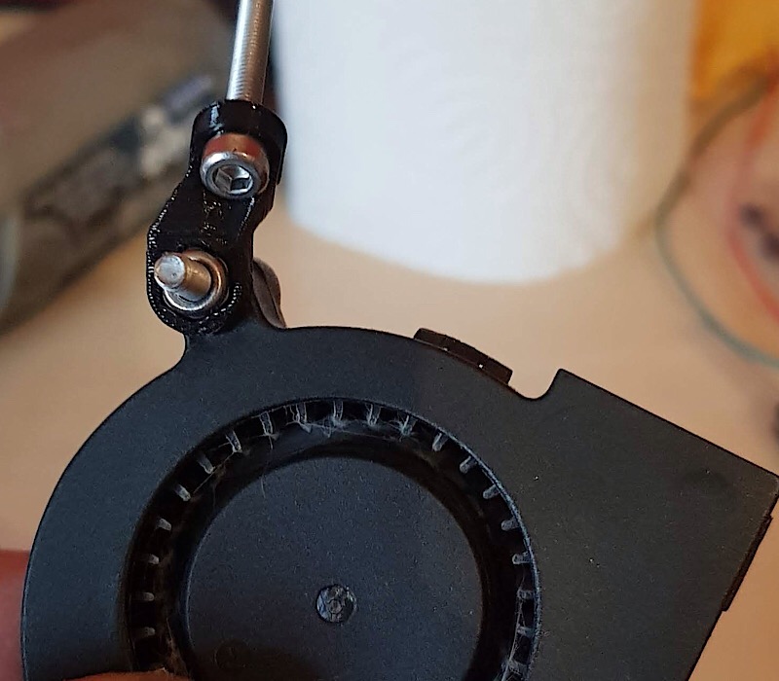
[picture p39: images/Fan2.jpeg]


### Wheel

insert 1 square nut into nut pocket

-   1x sq nut

insert short screw into hole (see photo)

-   1x M3x6mm (or 4mm or 8mm)

screw in just enough to catch threads of nut, but not go past flush Check that wheel can slide onto axle cleanly, then remove from axle

snap tread over wheel, first aligning the access holes Note that the wheel is not flush with tread by design, there is a small lip

### Shaft prep

If you ordered the Misumi custom shaft from link at top you can skip this section. Otherwise, you will need to cut some flats for grip.

The RC heli spindle is the perfect size and very light, but you can also cut your own from larger stock. If you have a raw cut end, lightly chamfer one end with file (just to remove any burrs).

Mark 15mm from the end with sharpie.

Grind a small flat, at least 4mm wide, into shaft 0.45mm deep (no deeper), centered at the 15mm mark. Go slow and measure frequently so you don’t go too far.

Do the same at 37mm from same end.

You can go wider than 4mm, such as using a bench grinder. I used a Dremel with cutting wheel.

Mark a line with sharpie along shaft to indicate flat orientation.

Next photo is using a spindle shaft from RC heli which is perfect size out of the box, and hollow so lighter. Be extra careful making flats since it is hollow. I only went about 0.3mm deep at 37mm mark since that needs a bit more strength.

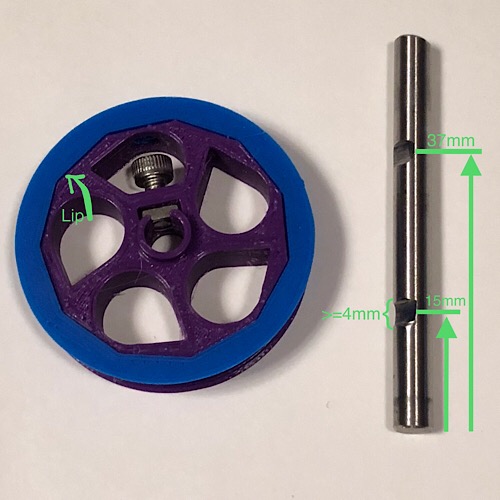
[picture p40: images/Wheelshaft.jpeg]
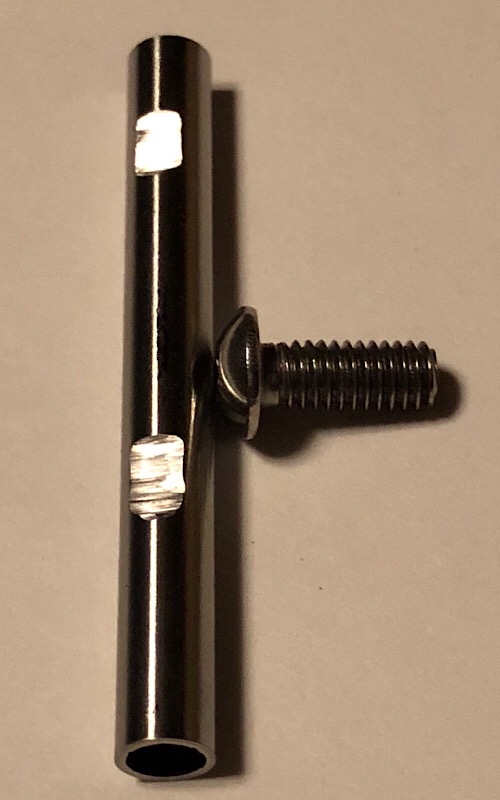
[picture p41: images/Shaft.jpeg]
||shaft

Assembly
--------

Slide shaft through wheel (do not tighten!), then Slide through Ecage F bearing Be careful to keep shaft straight so you don’t torque front bearing Slide through bondtech drive gear with teeth toward rear

-   1x bondtech drive

Finally slide shaft through Ecage B bearing until it is just flush with bearing, not protruding any Now while pressing wheel against cage F front bearing, tighten wheel screw onto shaft on flat by lining up mark Turn shaft so you can see mark and rotate Bondtech gear so set screw is aligned with mark Temporarily Insert piece of filament into Bowden to use for alignment Make sure hobb of gear is aligned with filament path Lightly press wheel against Ecage F and tighten Bondtech set screw onto flat Remove filament and check that you can turn shaft easily, even spins

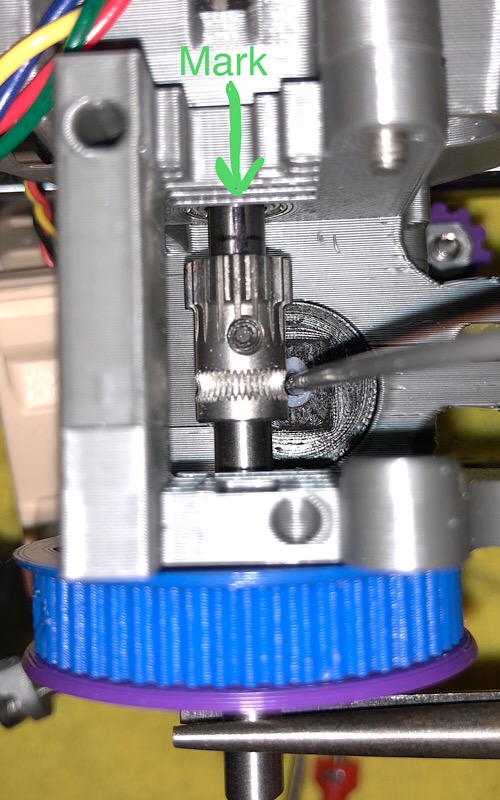
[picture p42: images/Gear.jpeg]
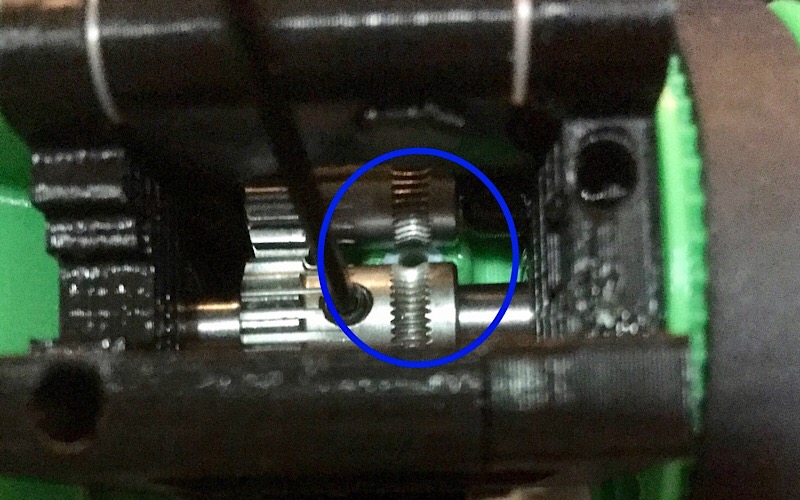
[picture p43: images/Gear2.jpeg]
 

Slide on spacer with flat side against wheel wrap GT2 belt loop over wheel

-   1x 140 GT2 loop

Use tensioner to prop up belt so it does not catch on next step

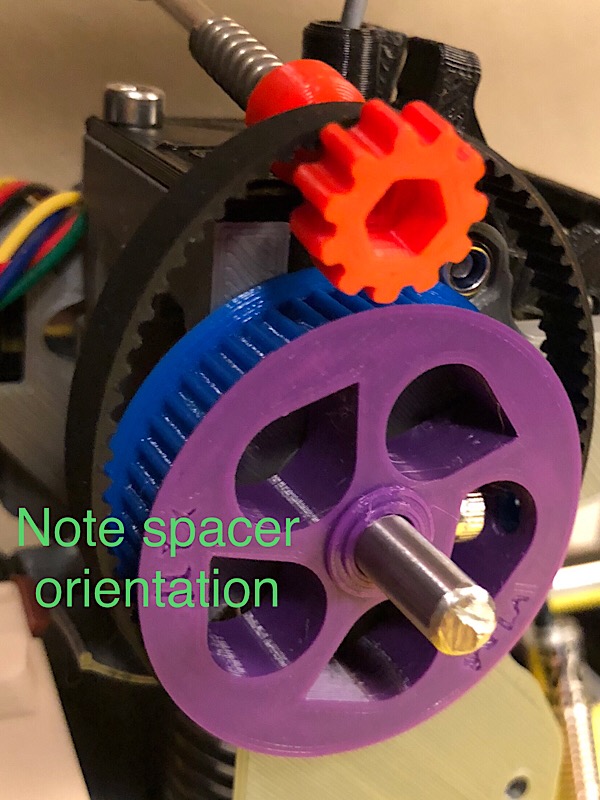
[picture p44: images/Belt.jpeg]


Slide spider bearing over shaft, up against spacer, watching the bottom leg does not snag belt, while also inserting anchor screw Screw spider onto cage F in hole below wheel snug but not tight

-   1x M3x18mm -&gt; temporarily, will switch to 20mm later

Remove tensioner prop and pinch belt to create loop to insert pulley and screw motor to spider loosely (orient motor so wires are on left, not like picture)

-   1x M3x18mm
-   1x M3x10mm

Make sure belt sits on pulley teeth, not collar First Snug up screws then back off 1/2 to 1 full turn. Rotate motor body clockwise to take up slack in belt loop. Do not over tension! Does not need to be tight like X and Y belts. I gently pinch motor and spider while tightening 1 and 2. First tighten short side screw, then top screw, lastly bottom anchor screw.

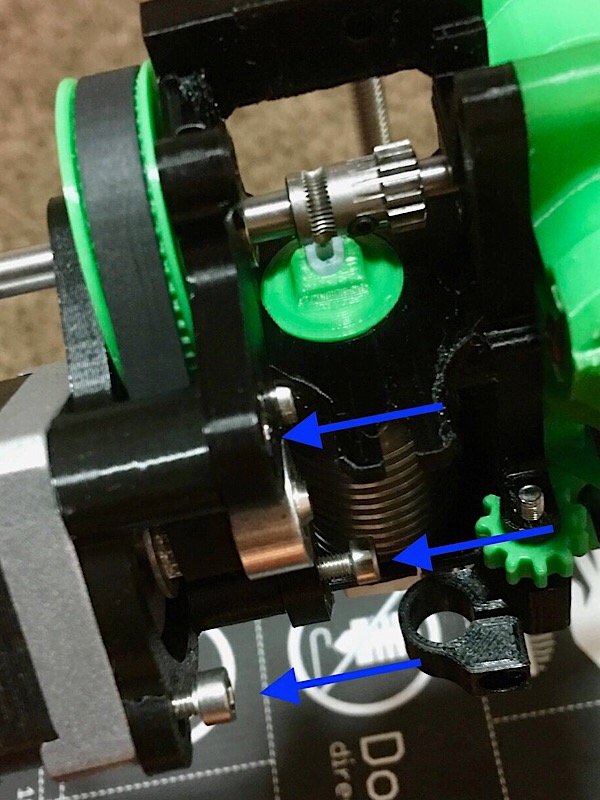
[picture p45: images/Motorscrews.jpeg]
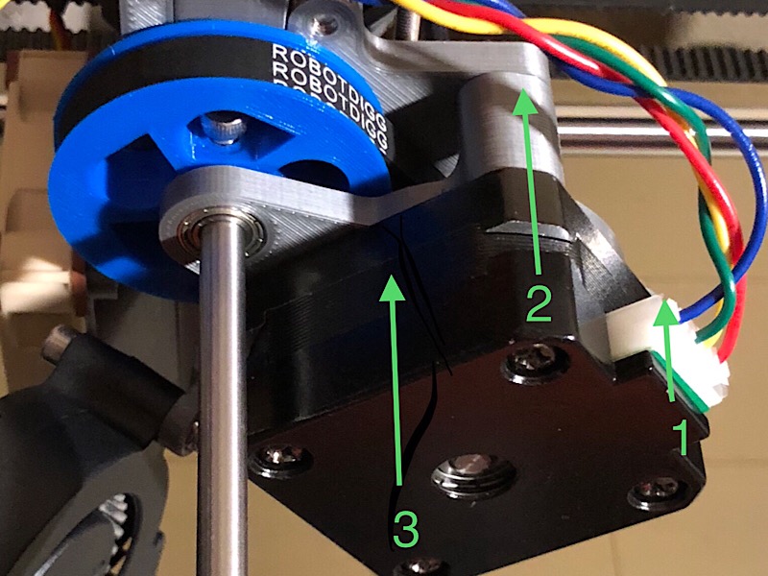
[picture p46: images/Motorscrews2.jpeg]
 

Slide cartridge into top and screw tight Add last screw to hold cover to cage

-   1x M3x10mm

Insert 40mm screw in top hole from cage B back with about 1mm tip protruding, just enough to hang first nylon washer Slide in idler and slide screw through most of idler, then add second washer and push all the way through and screw down \*lightly\*

-   1x M3x40mm
-   2x nylon washer

Screw head will not be flush!!

Screw Noctua onto cage b mounts

-   2x M3x12mm

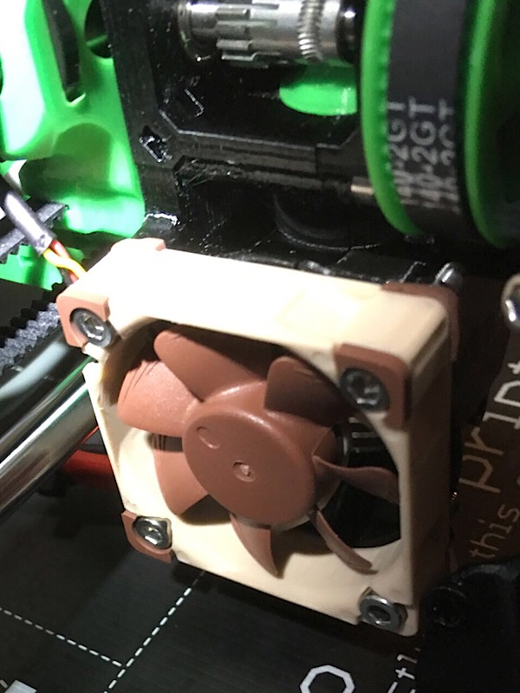
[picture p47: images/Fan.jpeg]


Screw fan onto bracket and rotate fan up a little.

-   1x M3x20mm -&gt; replace 18mm that was there

Keep screws a little loose. Attach nozzle, and screw onto bottom screw of Noctua shroud Rotate fan down into nozzle, then tighten bracket screw

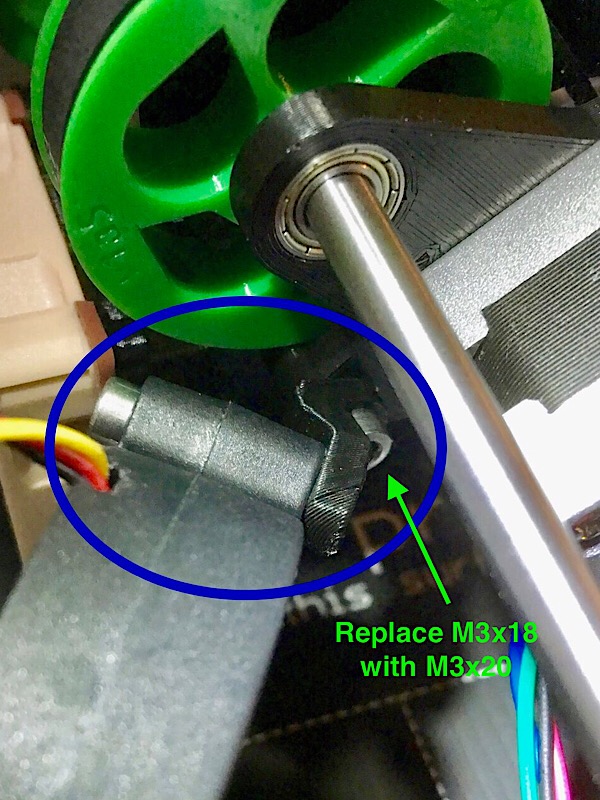
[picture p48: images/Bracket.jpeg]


Slip PINDA into holder with tip slightly above nozzle height as normal tighten medium (screw head almost flush)

-   1x M3x10mm

Optionally, route heater & thermistor wires up channel in back of cage B. Slip through hole and route out under shaft, away from idler

Slide entire extruder onto key block and slide down, making sure heater wires fit into channel on key Watch the top screw slides into mount on carriage Secure extruder using screw tabs on either side

-   2x M3x10mm

Tighten M3x40mm idler screw, but do not over tighten! Maybe snug then back off 1/2 turn. Make sure idler swings smoothly, but not so loose it falls down if you let go. Make sure Nyloc nut didn’t get pushed out and is not protruding from front face. Check the bondtec teeth mesh cleanly.

Slide tensioner screw head into bottom slot with spring below Pull up and hook knob into slot on idler Make sure two pivots on tensioner knob are in detents on idler (the arrows on top of knob should always point front to back)

Double check all screws are snug. Make sure all moving parts move freely

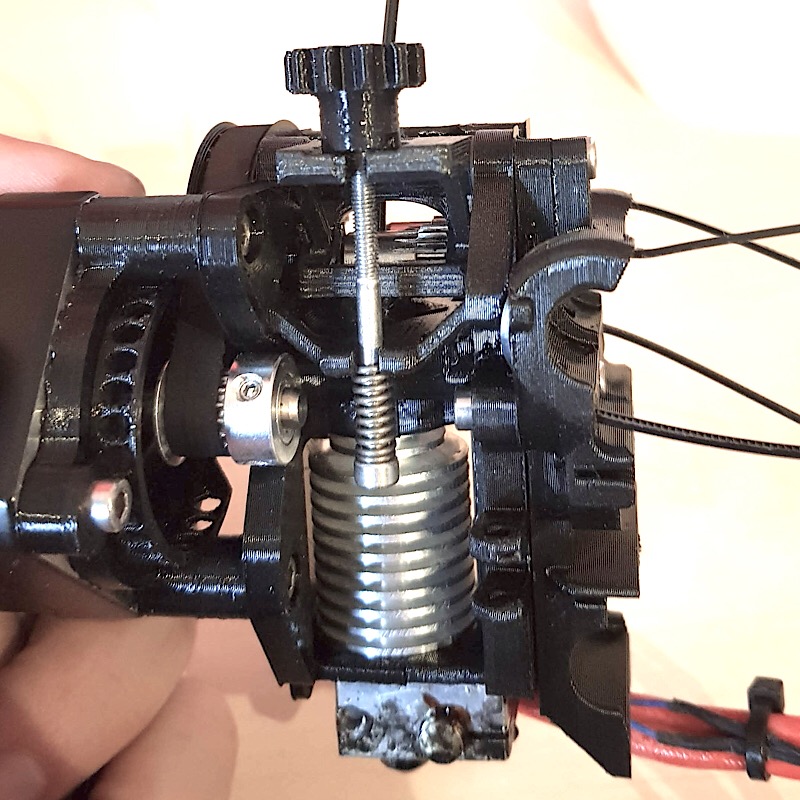
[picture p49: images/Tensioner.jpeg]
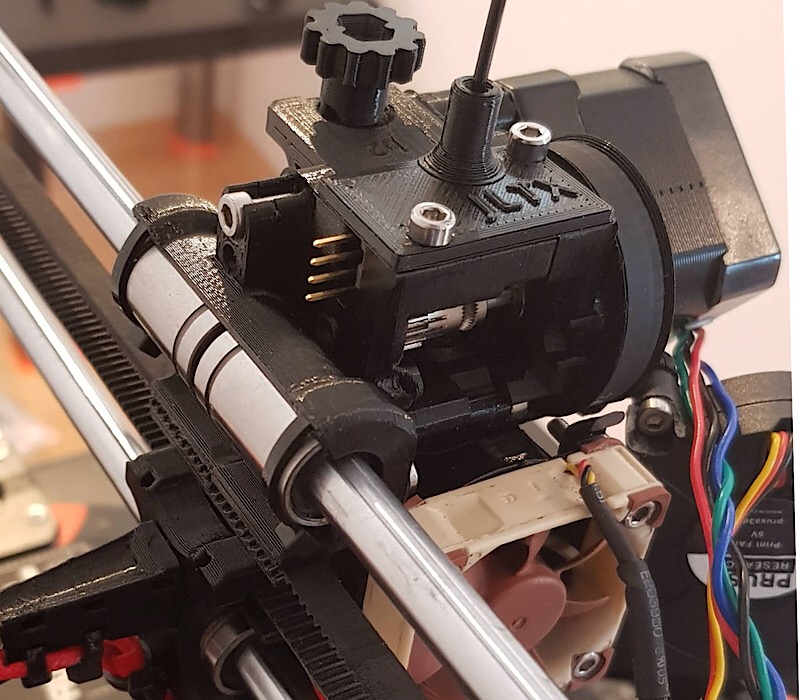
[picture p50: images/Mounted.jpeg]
 

### Cable management (one way, but do what you will):

-  Pinda: route wire up between top belt and top bearing.

Rotate Zip head down to lock into place (see pic).

-   Noctua: treat same as pinda (see pic).
-   Blower fan: route wire along top of Noctua, outside tab.
-   Motor: similar route as blower fan.

Insert zip into channel in back corner of Ecage B (there are two choices to pick from depending on route you chose). Capture Noctua, blower, motor wires. Route around side of carriage, over top belt toward sensor. Bring down filament sensor wire from top.

Optional: Insert M3x?? Screw into center hole on carriage to guide wires around left side (looking from behind). Zip tie down to X clamp

Tail:

- Pull along tail and zip tie down
- Also zip up heater cables underneath tail from below
- Can use screw access hole in tail to insert Nylon filament if using

Fin:

- Run along right side and zip through main center hole
- Snap one wire into each holder

Add spiral or sleeve

### Attach belt to carriage

Measure twice, Cut once.

Either install new belt or trim stock belt to fit new carriage. You want enough length to get all teeth engaged.

Fully insert in one side, the loop through both X ends (with motor slack). Pull snug and trim belt at innermost tooth. Slide in to belt holder and tighten motor.

-   do not over-tighten\*

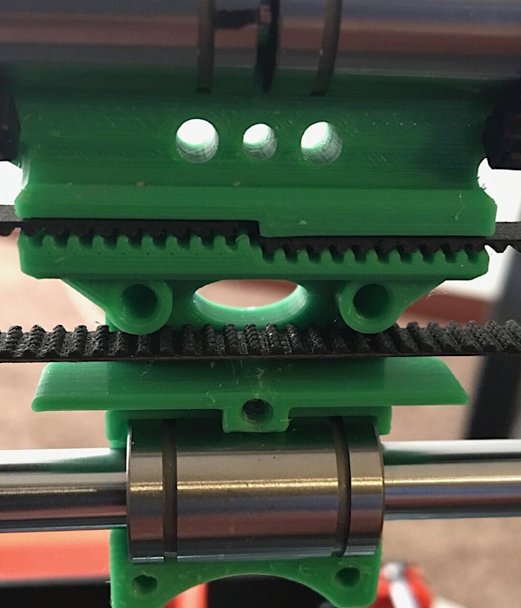
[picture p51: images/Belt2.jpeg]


Optionally, you can add a hobb cleaning wheel, for example printing TPU. Use an M3x30, add the collar, then a 20mm brush wheel, then hex nut. Fit screw tip into stirrup on CageB and snap head into clip on CageF

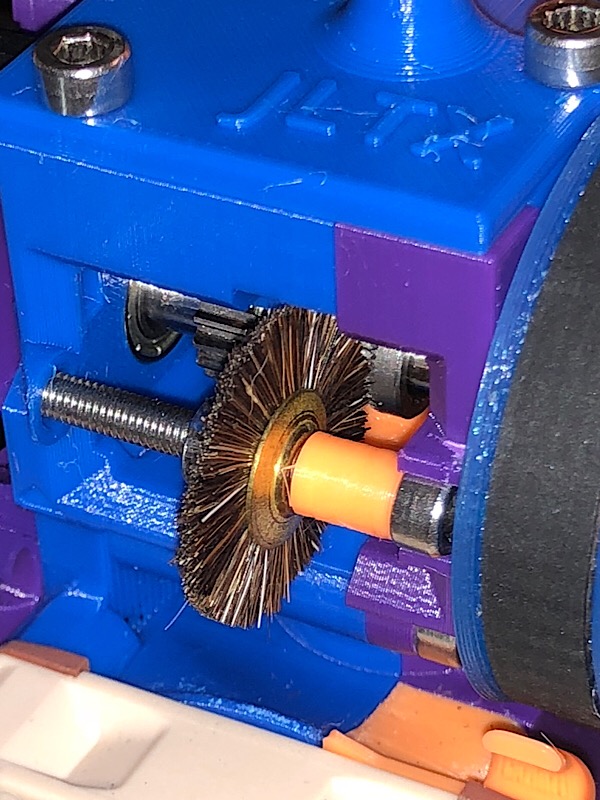
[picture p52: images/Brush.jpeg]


Tool-free Operation:
--------------------

To adjust PINDA height, e.g. after changing nozzles, turn PINDA adjust knob counterclockwise (looking down at bed) to lower PINDA (which increases nozzle clearance to bed). Each detent click is 0.1mm height change.

To adjust tension on idler, turn tensioner knob clockwise (looking down) to increase tension. Turn 1/2 turns only and make sure pivots are set in idler. There are indicators on the top of the knob aligned with the pivots. Hold screw head to keep it from turning.

To quickly disengage Bondtech gears (e.g. manual load / unload filament), just pull up from under idler edge (not the knob!) slightly until you can free filament. I brace my thumb on the filament cover. I use this to catch/hold the filament while I wait for nozzle to heat before fully loading.

To swing idler up for access to gears, unhook tensioner by lifting knob up slightly while sliding out of idler. Then drop slightly to release spring tension and pull tensioner out completely. Now idler gate can be swung all the way up. BE CAREFUL and watch pinda cable when removing and installing tensioner.

Slic3r Profiles
---------------

You can use the standard profiles. But here is an example to exploit more speed (remove .txt extension):

<a href="files/0.3mm_FastProto_Volcano.ini.txt">0.3_FastProto_Volcano.ini.txt</a>

Software changes:
-----------------

On first run, you should just need to do a Z calibration, followed by a first layer calibration. A full XYZ should not be necessary. Need to change E steps to 980 (see below)

Gcode: Get settings M503

Need to change E steps to account for gear ratio (3.5:1) M92 E980

Save settings M500

Change motor current, depending on your motor, if it gets too hot using stock settings: I found that I needed to reduce the default E motor current for my smaller motor. If it’s not getting too hot, leave it default (30). Example: M911 E24 ; set holding current lower M912 E24 ; set running current lower M910 ; commit new currents until power cycle

INFO: M910 - Reset and initialize the TMC2130 chips.

- Most setting changes won't go into effect until this code is sent.

M911 - Holding current M912 - Running current

- Set the above TMC2130 currents.  Must be given in current scalar values (0 to 63).
- Example:  M911 X14 Y20 Z30 E36

M913 - Print the currently set TMC2130 current values

I wanted to make it so that you only need to make some gcode changes to operate. This is mostly true. Unfortunately, due to the shorter stack, the filament unload sequence assumes the wrong amount to unwind and doesn’t properly cool the hot bulb which can cause it to stick in cartridge. You can simply unscrew the cartridge and clip off the end to free it (handy trick of skelestruder). But if you do frequent filament swaps, this can be annoying. So best option is to modify the sequence in firmware. Since you are recompiling, might as well set the E steps to 980. Following is a patch file for MK3 3.3.1 you can apply or follow manually to make the changes.

<a href="files/SPV1_3.3.1.patch">SPV1 3.3.1.patch</a>

<a href="files/SPV1_3.4.0.patch">SPV1 3.4.0.patch</a>

<a href="files/SPV1_3.5.1.patch">SPV1 3.5.1.patch</a>

- changes E steps, motor current, filament load/unload

- adds nozzle only pre-heat to menu, fixes variable type for clean compile with latest Arduino

Apply at Prusa-firmware level: patch -p1 -I SPV1_3.3.1.patch

This should apply directly to 3.3.1. IF you grab ToT it may not go cleanly.

If it fails, you will see .rej files that show which chunks it could not find. That is usually from them moving line number around too much.

You can just search and replace by looking at the context in the \*.rej file since it's just a text diff.

Note: if you went with the indirect sensor cartridge, you \*do need\* to make a change. See patch below.

To confirm it is working after flashing: got to Support menu / Extruder info

You will see Fil Xd 0 Yd 0

Insert filament manually and make sure Yd increases as you insert and decreases as you retract

If it changes the other way, you didn't get the sign flipped correctly.

If it doesn't move at all, check that the bearing spins freely. Also check that you can see both the filament sensor and the laser illuminator through the access port in I-lid

The laser is a small dot above the square sensor. If it is blocked, it cannot see the bearing.

### Editing Needed Below?

This patch is only for indirect filament sensor, changes sign of Y motion

```
diff --git a/Firmware/pat9125.cpp b/Firmware/pat9125.c
old mode 100755
new mode 100644
index 4894c85..5497467
--- a/Firmware/pat9125.cpp
+++ b/Firmware/pat9125.cpp
@@ -180,7 +180,7 @@ int pat9125_update_y()
                        if (pat9125_PID1 == 0xff) return 0;
                        int iDY = ucYL | ((ucXYH << 8) & 0xf00);
                        if (iDY & 0x800) iDY -= 4096;
-                       pat9125_y -= iDY; //negative number, because direction switching does not work
+                       pat9125_y += iDY; //negative number, because direction switching does not work
                }
                return 1;
        }
```

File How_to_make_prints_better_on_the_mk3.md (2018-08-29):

Ever since issue 602 was raised there's been considerable investigation into identifying the aspects of the Prusa i3 MK3 that affect the surface quality of the printed parts. A number of potential problems have been found.

The following is a list of modifications that I've made to my MK3 to make the prints look better... without replacing the whole thing. You should consdider it a list of identified issues and their potential solutions. In addition to the items shown here there are further changes that will not be listed in this article as they are more like reworks than fixes. Furthermore, 'very basic' issues like 'having the belts tight enough' or 'ensuring that the PEI surface is clean before printing', will not be covered here.

Note that all the parts I reprinted are PLA with at least 40% infill and 5 perimeters.

This is result of some of the modifications below. Note this is the same gcode file and filament. We need more volunteers to make test-prints for all of the fixes and workarounds.

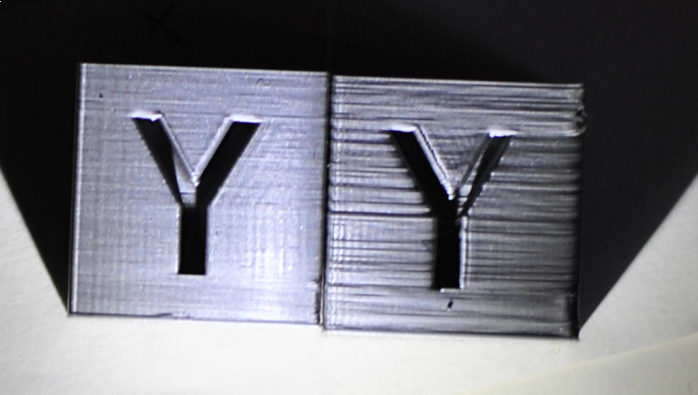
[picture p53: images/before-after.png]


Bearings
--------

This is mandatory on any machine. Your bearings need to have smooth linear motion without any 'crunching'. Loose tolerances that allow you to wiggle the bearings on your rods is highly undesirable. I've replaced the LM8UU bearings on my mk3 twice, the stock ones spat their balls all over my table after 40 hours of printing. The second, Chinese ones, did last a little bit longer, but they've had significant play in them since the beginning.

I suggest that you buy some high quality bearings. Unfortunately these may be pretty expensive and there would be no guarantee that they fit the rods supplied from Prusa Research without loose tolerance or 'play'.

A lower cost alternative is to make your own PLA bearings, which I find superior, but they are a lot of work to get right. I've put the instructions on making them in another article. [PLA bearings](PLA_bearings "wikilink")

Loose rods on Z axis
--------------------

It is important that your Z axis rods are not loose. You should check the Z axis printed parts, top and bottom, to ensure that they sit snugly and cannot be moved My stock z-tops allowed at least 0.5mm of play with the rods, which again, is highly undesirable. I suggest you to reprint the Z-tops if you experience something similar.

You can find improved Z axis printed parts here: [Improved_Z-axis_mounts_by_jltx](Improved_Z-axis_mounts_by_jltx "wikilink"). I've printed the Z-tops, to remove the play, and the Z-bottom (motor holder) because I was disassembling the printer very often and these made that process much easier. They are also more rigid, which is good.

Badly installed Z nuts
----------------------

One common issue with Z nuts is that many people install and tighten them in their X-ends BEFORE they have the whole X and Z axis assembled. I find this wrong because you need to ensure that the rods and trapezoidal screws are parallel. If you tighten the Z-nuts in place and then install the whole X assembly on the Z axis, things will bend, which is not good. To fix this little issue; ensure your Z axis is perpendicular to the X-axis, loosen the screws that are holding both of the Z-nuts, and then tighten them again. This will release any pressure that is being put on the rods or trapezoidal screws.

Extruder assembly problems
--------------------------

### Loose hotend in extruder assembly

Move the X carriage all the way to the left, push on your nozzle, holding the extruder with your other hand. The nozzle should not move at all. I mean it really really should not move, even if you put a quite bit of force on it (just don't break the printer). Repeat it from all the sides, and ensure there is NO wiggle. If there IS wiggle, this will cause a number of problems. On my printer, there was wiggle, and I have also seen how the hotend moves when the printer extrudes / retracts.

I've found a workaround that solves this issue pretty well. Disassemble the extruder assembly (remove the radial fan, unscrew the two screws, unscrew the two screws holding the front part on Noctua). Pull the hotend out of the extruder assembly and find some stretchy tape - I've found that PVC electricians tape works best. Put something like 4 turns of the tape on the e3d's neck. Put some more tape around the bottom of the e3d heatsink, but make sure that it does not touch the heatblock. Then find a knife and cut the tape on the bottom so it only wraps around the last rib of the heatsink. It should look something like this now:

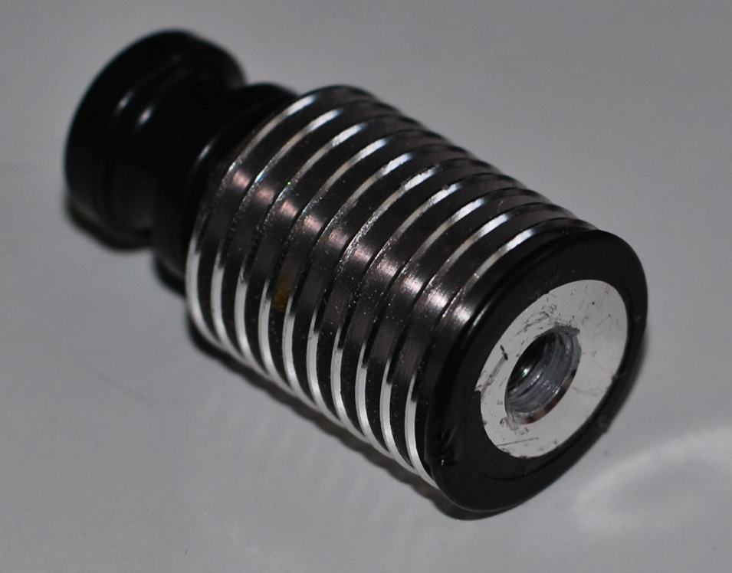
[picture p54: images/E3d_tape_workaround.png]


In addition, i'd recommend reprinting the extruder assembly using some less flexible filament than PETG and with additional infill and perimeters.

Since you have the extruder disassembled now, it is a good idea to look at the next section before reassembling.

### Loose PTFE tube in the hotend

The e3dv6 comes pre-assembled, but it's missing one important thing; the locking washer that locks the PTFE tube fitting so the tube can't be pulled out. To solve this I preheated the hotend and made sure that the PTFE tube is inserted all the way down. You need to hold the hotend by the PTFE tube that is sticking out and then pull the black lock thing up, so it locks the PTFE tube in place without any play. It is also good idea to put the locking washer in there, but if you do not have a way of printing them or you do not want to wait until they arrive, you could just use some copper wire, or something similar and tie it below the black lock thing (so that you are unable to press it down anymore).

Reassemble the extruder again and tighten the screws. Make sure that everything is snug this time and your extruder does not suffer from the hotend wiggle anymore.

Extruder gears
--------------

### Drive gears not meshing properly

In order for gears to mesh correctly it's important that the distance between their centre of rotation remains consistent and correct. In the MK3 there are a number of aspects that influence this distance such as: idler springs, variation in filament diameter, loose mounting of the idler itself and loose mounting of the idler assembly. As a result of these variation in distance between the bondtech gears will change over time which causes a number of issues since they are rarely able to mesh correctly when setup in this way. This poor gear meshing causes pressure oscillations in the hotend which will result in inconsistent extrusion.

This is the test object that proves they are problematic (upper one):

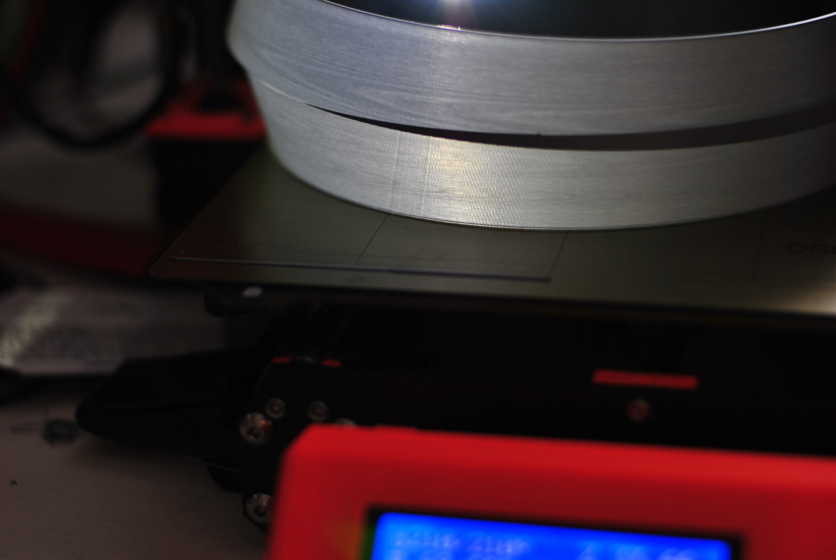
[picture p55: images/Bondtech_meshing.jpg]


The wood pattern is caused by the drive gears, there is the same number of the '&lt;&lt;&lt;&lt;' as there are teeth on the Bondtech gears. The simplest workaround is to disable them, which could be done by flipping the Bondtech gear on the motor shaft. You will not lose any grip on the filament, there is just no reason to have a powered idler.

### Biting into the filament

This issue affects a lot of printers, but it is usually less pronounced than on the mk3. Since we are on the hunt for surface finish perfection, we need to do something about this. As the extruder gears bite into the filament, the filament going to hotend is not ~1.75mm cylinder anymore. It has those not-so-tiny ripples on it and they cause pressure fluctuations in the hotend. There is not much to do about this. The only slight solution is to loosen the idler screws so the extruder gears just have barely enough grip on the filament causing it to bite less and making the issue less pronounced

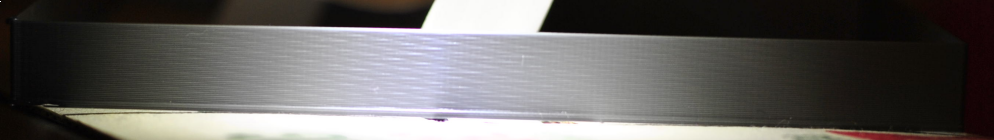
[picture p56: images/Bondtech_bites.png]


This regular pattern observable on 100mm single wall spiral vase cube is caused by this. There is the same number of the moire lines as there are the tiny 'teeth' on the extruder gear.



What I've done is take my extruder gear to a machine shop and got rid of the hobbed part of the extruder gear.

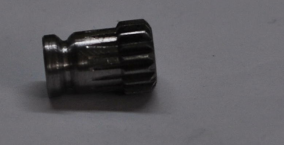
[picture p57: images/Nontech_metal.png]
File:Nontech metal.png


My prints do not suffer from this pattern anymore, and it still provides enough grip to the filament. However, there needs to be some further research to make those gears properly.

You also need to replace the hobbed idler with a bearing, similar to the mk2 style.

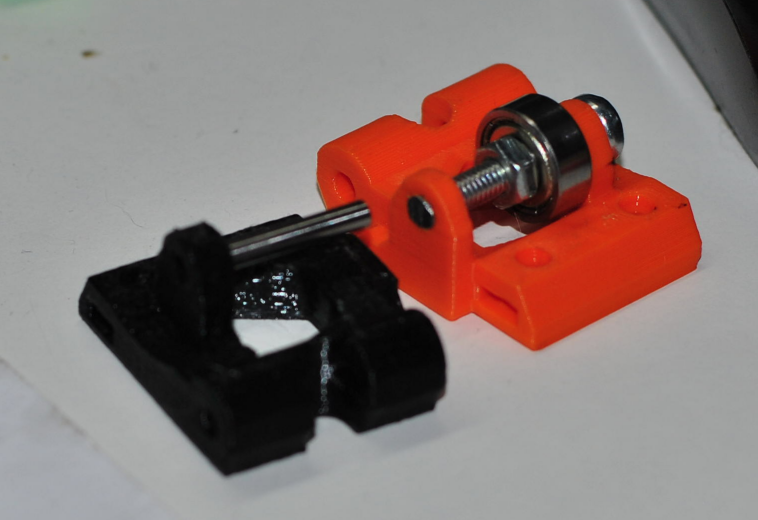
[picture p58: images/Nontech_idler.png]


They are published on Thingiverse here: <https://www.thingiverse.com/thing:2965241>

Hotend Cooling Issues
---------------------

Tests on the MK3 with Bowden extruder found that the heatbreak cooling solution is not effective without modifications. This is less apparent with a direct drive setup due to back pressure building much faster in that scenario; however, it **does** still affect direct drive users. The following tests and examples were done on a Bowden system to abuse its larger exaggeration of these effects and prove the theory out. Please keep that in mind as you read forward.

### Testing Methods
<ol>
    <li>After a period of no extrusion (a few seconds) filament in the cool end of the heatbreak gets too hot and becomes soft. This causes sticking and leads to back pressure. Upon starting extrusion manually, this is presented as:
        <ol type="a">
            <li>Initial extrusion is very weak and slow due to stuck filament. Back pressure is building during this phase,</li>
            <li>Extrusion suddenly becomes very heavy. Back pressure has built to a point to overcome the sticking in the heatbreak and the extra pressure is released out the nozzle,</li>
            <li>Flow evens out and remains even as long as extrusion continues. As long as the filament is moving, it remains cool enough above the break that a sticking issue doesn't happen.</li>
        </ol>
    </li>
    <li>3DBenchy is particularly afflicted by this problem in the upper cabin area. To speed testing the cabin area was cropped away into its own STL. Results are as follows:
        <ol type="a">
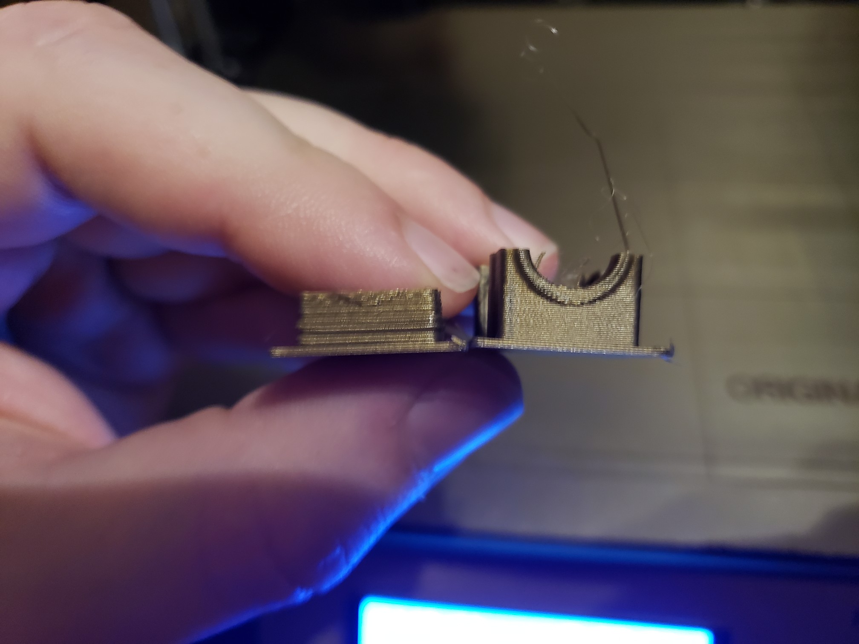
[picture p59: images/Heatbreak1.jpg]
            <li>In the image, the left hand cabin piece was printed with the stock Noctua fan and R2 extruder parts. It's hard to see the under extrusion; however, you can see the waves of over extrusion that followed after. The right hand cabin piece was printed using a 12v fan powered directly off the 24v input into the Einsy. This is obviously **not recommended**; however, for the purposes of this test it showed that the under/over extrusion cycle was fixed by applying more cooling to the heatsink and thus cooling the heatbreak further.
            </li>
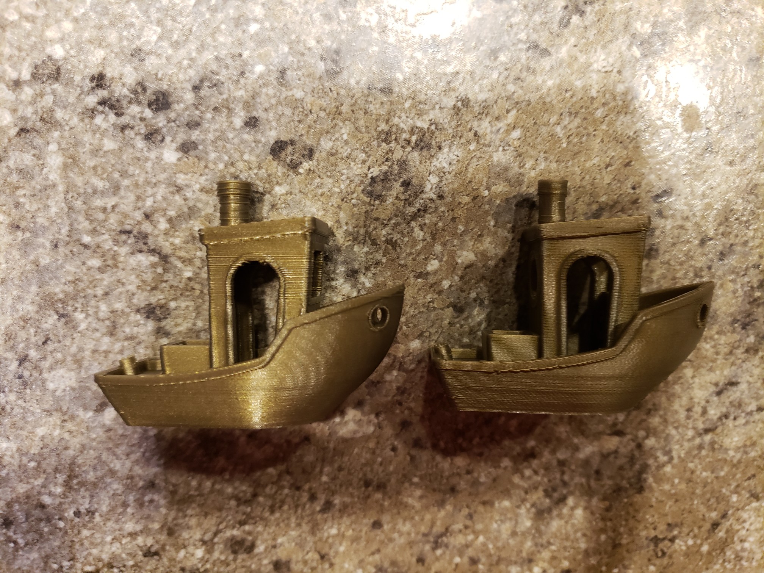
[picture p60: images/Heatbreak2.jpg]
            <li>In the image, it was found that even with the better cooling, the upper parts of the cabin on the left hand Benchy still had this issue due to Slic3r's “automatic cooling” feature slowing down those layers. Automatic cooling works by decreasing the print speed to allow fresh filament time to cool before another layer goes on top of it. The effect can also be seen in the smokestack. This is ultimately due to the heatbreak not being cool enough on the cold side and filament was lingering long enough to heat up and soften. To prove this out, the right hand Benchy was printed with automatic cooling off and speed at 200% to ensure the filament would have no chance to warm and stick. Artifacts were introduced by running at this speed; however, we can see the artifact in question has completely vanished.</li>
            </li>
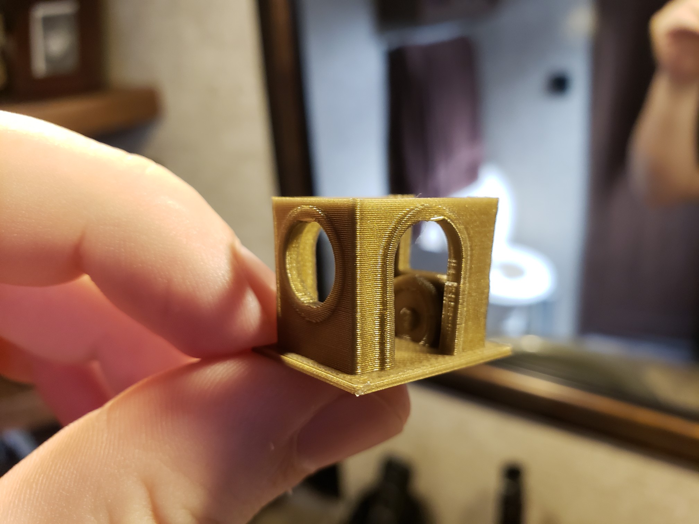
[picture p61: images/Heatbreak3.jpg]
            <li>In the image, you see a Benchy cabin after installing a 40mm 24v fan directly to the 24v supply (the standoffs on the Einsy 24v input were used so wire routing would be similar). This shows that by increasing the fan output compared to the above tests, we see even more benefit and can drop back down to normal print speeds.</li>
            
        </ol>
    </li>
</ol>

### Cooling Improvements

Several things can be done to improve the heatbreak cooling situation, listed in order of benefit:

1.  Prusa has released R3 extruder parts specifically addressing this problem. They allow more airflow around the heatsink, less back pressure on the very weak Noctua, and a venturi booster vent allowing for increased throughput. **This will greatly augment the other things listed below! Most of these issues are caused by bad R2 design!**
2.  Replace the weak 5v Noctua fan with a 24v 40mm equivalent. Static pressure should be prioritized over CFM when making your fan selection. This can be wired directly to the 24v input standoff on the Einsy board to keep a similar wiring situation to stock. **You will likely fail self test until a method is found to monitor RPM with these higher voltage fans.**
3.  Insulate the hotend heater block with ceramic tape. This offers several benefits, in this case in particular though it will help isolate the heater block from the heatsink above it. The radiant heat from the block transfers into the heatsink above raising its temperature significantly. Preventing this heat transfer will allow the heatsink to wick away heat from the break more efficiently.

### Direct Drive Before and After

Coming soon.

X ends not strong enough
------------------------

You may notice that when you put some pushing force on the extruder carriage, the X-ends start to twist, even the slit that is used to make the bearing insertion easier starts to open. It is a good idea to reprint these too. There are some better designs involving easier belt tensioning and providing some extra rigidity. For example these: https://www.thingiverse.com/thing:2964026

Belts rubbing
-------------

Belts sides rubbing on the motor pulley or the idler are problematic too. You may need to adjust this, or even buy some proper idlers that are designed to prevent this.

Firmware
--------

The stock firmware does suffer from some timing issues TODO: put some reference on logic analyzer results here? This is what Klipper fixes. Until this is fixed in the stock firmware I suggest using Klipper, although it is not exactly user-friendly daily-driver yet, guys are working hard on it.

Linearity correction
--------------------

Linearity correction needs to be done on all axes but particularly the extruder axis as stepper nonlinearity may result in more inconsistent extrusion. Non-linearity on XY plane will cause vertical ripples on the print. See the top left cube, this is something that is clearly not caused by belts nor ringing. This needs to be fixed now, we do not have a proper solution yet. Both klipper and stock firmware do support linearity correction, but stock firmware suffers from other issues, and klipper does not yet support setting linearity correction value during print.

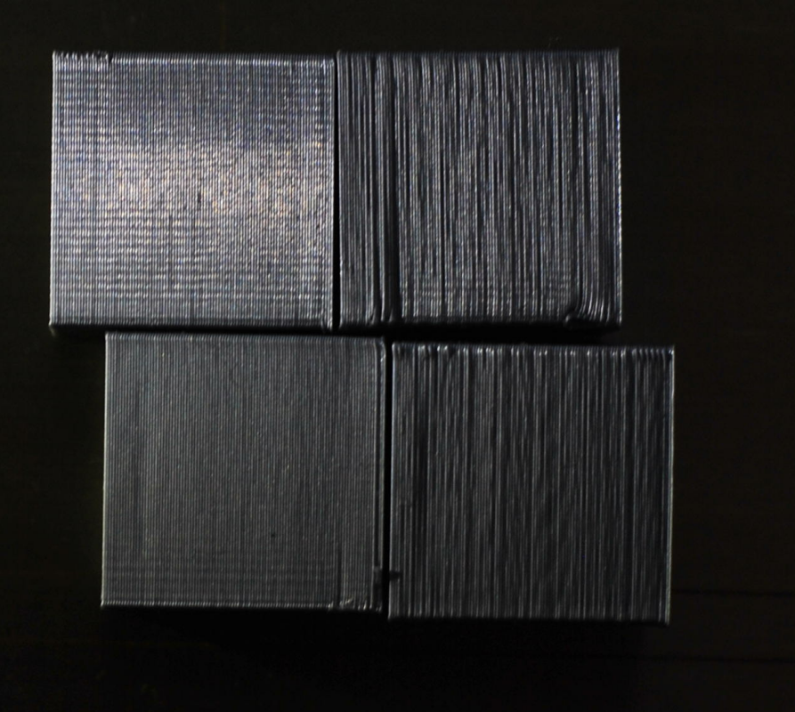
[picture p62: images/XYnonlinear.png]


Replacement feet
----------------

The stock rubber feet included with the MK3 tend to make vibration problems worse. Many users have found much improvement by replacing the stock rubber feet with rigid (or significantly more rigid) feet of some type.

The image below was printed half way up using the stock rubber feet, and the other half was printed with rigid feet:

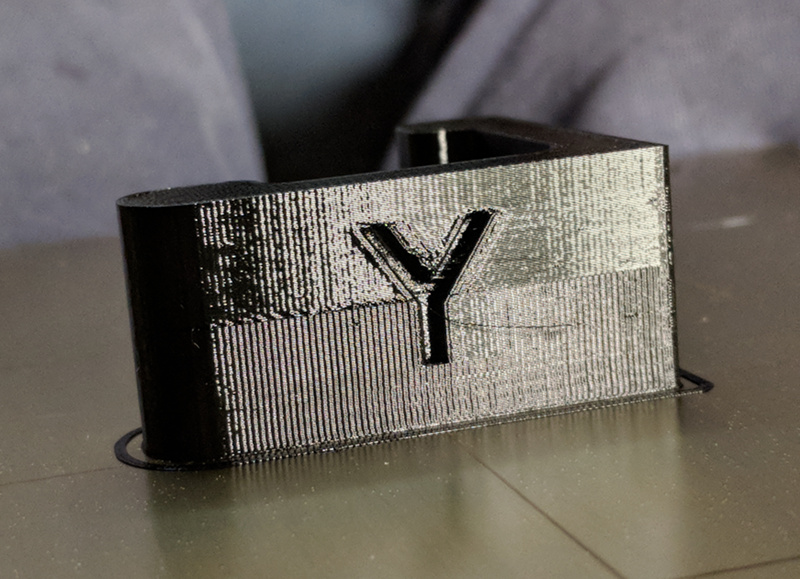
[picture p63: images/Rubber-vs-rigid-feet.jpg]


There are already a couple options out there for hard feet:

-   <https://www.thingiverse.com/thing:2805753>
-   <https://www.thingiverse.com/thing:2802540>

Either of these modifications is very easy to implement and will improve surface quality; however, they will make your printer a bit more audible.

### The Rigid vs Absorption Argument

More details need to be added here on why rigid feet outperform vibration absorbing ones. It's a common misconception that vibration absorbing springy feet will help print quality, when they are primarily for acoustics.

The theory on this is that the rubbery feet causes mechanical reverb.

Flipping the Y belt 90°
-----------------------

This needs further research

Nozzle polishing
----------------

This needs more testing

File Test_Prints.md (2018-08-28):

This page contains links to various STL and G-code files that may be useful in troubleshooting or evaluating the performance of your printer.

-   [3D Benchies](https://github.com/PrusaOwners/test-tools-and-objects/tree/master/objects/kwaad2/Benchy), sliced for several different filaments. These benchies were used for testing of various mechanical and firmware improvements during troubleshooting of the Prusa Mk3 inconsistent extrusion issue.

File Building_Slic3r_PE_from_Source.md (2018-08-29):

This page is a work in progress, please use at your own risk until completed.

Linux
-----

### Ubuntu 18.x and 16.04

```
#!/bin/bash

## Build Slic3r P.E. from source

## install system dependencies

apt-get update && apt-get install -y \
    build-essential \
    cmake \
    cpanminus \
    freeglut3-dev \
    git \
    libboost-all-dev \
    libboost-filesystem-dev \
    libboost-system-dev \
    libboost-thread-dev \
    libcurl4-openssl-dev \
    libeigen3-dev \
    libextutils-cppguess-perl \
    libextutils-typemaps-default-perl \
    libextutils-xspp-perl \
    libglew-dev \
    libgtk2.0-dev \
    liblocal-lib-perl \
    libmodule-build-perl \
    libopengl-perl \
    libtbb-dev \
    libwx-glcanvas-perl \
    libwx-perl \
    libwxgtk-media3.0-dev \
    libwxgtk3.0-dev \
    libxmu-dev \
    libxmu-dev \
    wx-common 

## WX requires a X DISPLAY to run its tests.   Configure this appropriately
## if you plan on build with gui funcionality
#export DISPLAY=:0.0
export DISPLAY=192.168.5.33:0.0

## if compiling headless add these: 
## apt-get install -y mesa-utils and libgl1-mesa-glx

## clone Slic3r from Prusa3d
git clone https://github.com/prusa3d/Slic3r.git
cd Slic3r
git checkout -b origin/master

export LDLOADLIBS=-lstdc++
perl Build.PL
perl Build.PL --gui

mkdir build && cd build
cmake .. -DCMAKE_BUILD_TYPE=Release
make
ctest --verbose
```

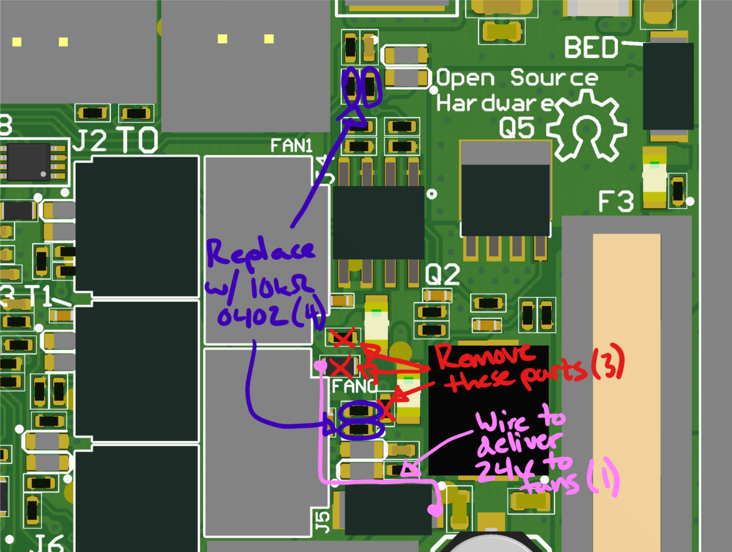
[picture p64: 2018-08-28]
images/Einsy_fan_rework_instructions.png

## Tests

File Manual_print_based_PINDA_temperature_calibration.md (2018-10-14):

This is valid for MK2.5 and MK3 and newer.

Background information
----------------------

On the Original Prusa i3 MK2/s and MK3 printers, instead of a traditional endstop switch, the Z-axis uses a sensor called a “PINDA” probe. The PINDA probe senses the proximity of the steel print sheet and triggers when it is within some distance of this sheet. Depending on the temperature of the PINDA sensor, the trigger distance might be higher or lower. The MK3 PINDA has a built-in thermistor that allows the controller board to determine the approximate temperature of the probe and roughly compensate for this in software. The MK2/s has no such thermistor, so no compensation is possible there.

To achieve this temperature compensation. the MK3 firmware uses a small table stored in EEPROM. This table stores offsets (in usteps) from a baseline triggering distance measured at 35C. Each entry in the table represents a 5C offset from the previous measurement (so temperatures of 40C, 45C, 50C, 55C and 60C). The offset for 35C is not stored and is the baseline value to which the other offsets apply (we can consider its offset to be “zero”). When the MK3 was first released , it used a fixed pre-populated temperature calibration table. Although the initial launch-date firmware included an automatic temperature offset calibration routine, for many users this yielded results worse than the default table.

Since product launch, there have been many improvements in this area; Prusa has incorporated two GCODEs (both contributed by forum user stahlfabrik) that solve problems with the PINDA measurement and make it possible to fully compensate over the PINDA temperature range, even if this compensation requires a negative offset value. In addition, the table in EEPROM is now populated with zeroes by default (so no compensation is applied). There is a setting in the printer menu that you can toggle to activate or deactivate temperature calibration. This setting is “off” in the factory default configuration. The reason for the changes to the temperature compensation feature is that it is better to have no compensation than bad compensation. With the previous design, some unlucky users found that the compensation worked in the opposite direction, making temperature-induced error worse instead of better.

With the current firmware, a badly calibrated PINDA is an absolutely unnecessary problem that you can get rid of easily. The approach suggested here will allow you to populate the PINDA temperature compensation table so that you get repeatable, accurate results across the expected PINDA temperature range. This calibration procedure takes two to three hours and is easy to perform. Although you can try the build in automatic temperature calibration, for me it has not yielded good results (although in fairness, I have not tried it for some months).

So when do you need to do a temperature calibration? If you find that your perfectly dialed in Live Z value is not correct when doing back-to-back prints or that it sometimes works, but other times does not. If you know or suspect this temperature variation to be the source of your error, then you should go through the calibration process described here.

Step by step - manual print based PINDA temperature calibration
---------------------------------------------------------------

The process takes only an evening and is not hard to do. The following steps have to be performed:

1.  [Prepare GCODE files](#prepare-gcode-files "wikilink")
2.  [Disable temperature calibration](#disable-temperature-calibration "wikilink")
3.  [Find Live Z value for each temperature](#find-live-z-value-for-each-temperature "wikilink")
4.  [Caculate offsets](#calculate-offsets "wikilink")
5.  [Store offsets in EEPROM](#store-offsets-in-eeprom "wikilink")
6.  [Enable temperature calibration](#enable-temperature-calibration "wikilink")
7.  [Set Live Z to the 35C value](#set-live-z-to-the-35c-value "wikilink")
8.  [(Optionally) verify temperature calibration](#optionally-verify-temperature-calibration "wikilink")

### Prepare GCODE files

[1st_layer_35C.stl](files/1st_layer_35C.stl "wikilink") is a very simple STL that consists of a rectangular shape that is 0.2mm high (any rather large 1st layer will do:-)). You import that to your slic3r and use your favorite (PLA) profile to slice. When you have the gcode file on disk (suggested name: “1st_layer_35C_PLA.gcode” or similar), open it in a text editor and modify it so you can use it for the manual temperature calibration process. The change you will be making is to add the M860 g-code. This g-code instructs the printer to wait for the PINDA to reach some temperature or beyond, either cooling (reach temperature or below) or heating (reach temperature or above).

Here is a snippet that I use for the 35C gcode:

```
...
M83  ; extruder relative mode
; cooldown
M104 S0 ; set extruder temp
M140 S0 ; set bed temp
G28 W ; home all without mesh bed level
G0 Z100 ; Cooling PINDA position
M106 S255 ; Turn fan on
M860 S30; Let PINDA cool down to 30C
M107 ; Turn fan off
; warmup
M104 S215 ; set extruder temp
M140 S60 ; set bed temp
M190 S60 ; wait for bed temp
M109 S215 ; wait for extruder temp
G0 X50 Y50 Z0.15 ; this is a good PINDA heating position
M860 S35 ; put here the temperature that you want to calibrate
; start the print
G28 W ; home all without mesh bed level
G80 ; mesh bed leveling
...
```

You can see the “cooldown” section, where I let the PINDA cool down 5C below the start temperature. There is also the “warmup” section where I set the bed and heater and then wait for the PINDA to reach the start temperature. Note that both sections use the M860 command. When the printer receives the M860 command, it checks if both heatbed and nozzle heaters are off. If so, it treats the M860 command as an instruction to wait for the PINDA to cool down, and will wait until the PINDA temperature is at or below the specified value. Otherwise, it treats this command as instruction to wait for the PINDA to warm up, and will wait until the PINDA temperature is at or above the specified value.

Once you have edited the file, make a few copies of it, renaming to ...40C.gcode, ... , ...60C.cgcode. In each file set the cool-down and the warm-up temperature values accordingly. Note that to reach the higher PINDA temperatures you may have to increase bed temps as well.

Here is what I use:

| PINDA target temp | Used bed temp |
|---|---|
| 35C | 60C |
| 40C | 60C |
| 45C | 60C |
| 50C | 80C |
| 55C | 90C |
| 60C | 100C |

### Disable temperature calibration

There are two steps you should do to clear the old temperature calibration values from the table and turn PINDA temperature calibration off:

1.  In the printer menu, turn the setting for “Temp. Cal.” to “off”.
2.  Use the terminal to your printer to send the command “M861 Z”. This sets all offsets to zero. You can verify that the values were cleared to zero by sending “M861 ?”. This g-code command will instruct the printer to output the current offsets in the EEPROM table.

### Find Live Z value for each temperature

Now comes the fun part. Load a PLA filament with a color that is conducive to observing the first layer properties during live-Z adjust (makes it easy to see the gaps and the surface texture). Print the first file (the 35C gcode) and dial in Live Z. The goal here is not necessarily to achieve the best/optimal first layer - but that you hit a first layer with properties that you will be able to reproduce with the other five gcode files that you will print later. The procedure that I follow is to raise Live Z a bit, then lower it down, until there are just no more gaps in-between the extruded strands. When I take remove that first layer from the print bed, I check to make sure that I do not see any direct light shining through gaps between the strands. Usually, it is totally achievable to hit that spot in just one try, so this process should proceed rather quickly.

Repeat this process using the g-code files for all the temperatures. For each temperature, note the live Z value that gave the desired results.

### Calculate offsets

I use a spreadsheet to calculate the offset values, but any calculator will do. Prusa has written “my” formula in a quite concise way on their wiki (link below), so I will just reproduce here:

```
usteps(T) = (live_adjust(35) - live_adjust(T)) * 400
```

The ustep values have to be integers, so round them off. Be careful to keep track of the sign; the sign is important! I mostly get negative values, but others often get more positive values.

### Store offsets in EEPROM

To store the values to the EEPROM, we use that first new code again: M861

To store -5 for the 40C value, you send the printer “M861 S-5 I0”. And as another example, to store 11 in the 45C offset value, sou send “M861 S11 I1”. So, “I” denotes the index into the EEPROM table, ranging from 0 for 40C to 4 for 60C - remember the value for 35C is the reference point and thus always zero.

By the way, if you want the old standard EEPROM table, you can set that with “M861 !”. I already mentioned that “Z” zeroes the table and “?” queries and prints the table.

### Enable temperature calibration

Now that our EEPROM table is full of reasonably accurate calibration values, we should re-enable temperature compensation in the printer menu. Got to “settings” and enable “temp. cal.”.

### Set Live Z to the 35C value

As the last step, you should set live Z now to the value that you found out when printing the 35C gcode file. It is also fine to now fine tune that live Z value for perfection - tell me more about it;-)

### (Optionally) verify temperature calibration

If your Prusa i3 MK3 runs at least version 3.3.1 you can use [Temp_cal_veri_v5.gcode](files/Temp_cal_veri_v5.gcode "wikilink") gcode file. The purpose is to have a printable test to verify that the values in your EEPROM value are good. The Gcodes prints six squares in one go, on the same plate. This takes a while because the PINDA has to cool down in between printing of each square. You just have to watch and wait. The top left square is printed with a PINDA temperature of 35C, right next to it is a 40C square printed and so on. So the squares are:

```
35C 40C 45C
50C 55C 60C
```

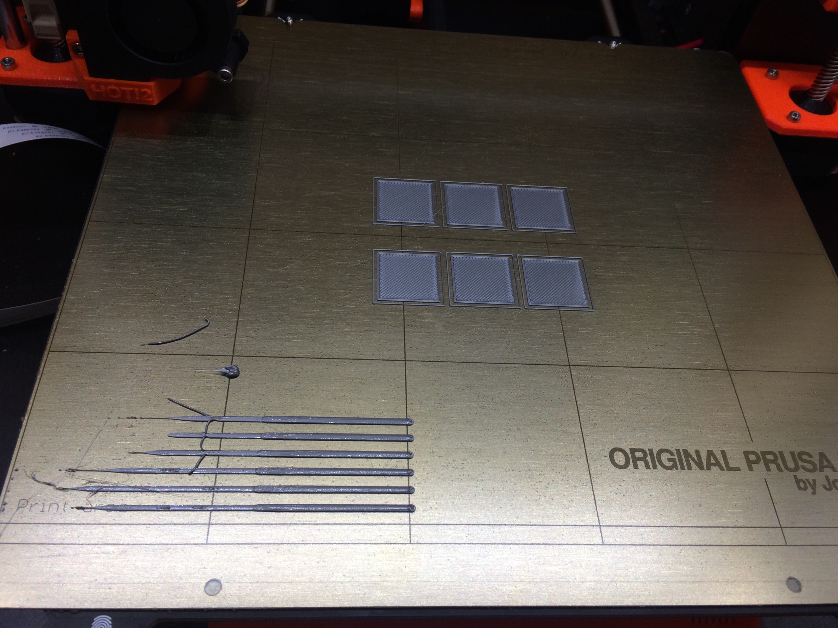
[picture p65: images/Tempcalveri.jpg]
Here is picture of how that print looks like: 

You can visually inspect the squares to make sure that each first layer looks good.

How to take advantage of the temperature calibration table
----------------------------------------------------------

So now that you have calibrated the temperature compensation table, you need to make sure that your PINDA is always in the temperature range of 35C to 60C before the printer homes and does the mesh bed leveling. A very easy way to do that is to use the code M860 code again. Because the PINDA calibration starts at 35C, we just need to insert an M860 g-code to tell the printer to start a print only when the PINDA is at or above that value. The g-code snippet below shows how to do that, for the Slic3r slicing software (put this in your Start g-code in the printer definition). Note that the M860 occurs **after** the bed and nozzle heaters are turned on. We want this because we want the printer to check the PINDA temp is at **or above** the specified value.

```
G28 W ; home all without mesh bed level
M104 S[first_layer_temperature] ; set extruder temp
M140 S[first_layer_bed_temperature] ; set bed temp
M190 S[first_layer_bed_temperature] ; wait for bed temp
M109 S[first_layer_temperature] ; wait for extruder temp
G0 X50 Y50 Z0.15 ; this is a good PINDA heating position
M860 S35 ; wait until PINDA is >= 35C
G28 W ; home all without mesh bed level
G80 ; mesh bed leveling
```

An Alternative Approach that Does Not Require Temperature Calibration
---------------------------------------------------------------------

If the above process seems too much, and you don't mind waiting a bit longer at the start of every print, then there is an alternate approach you can use that does not require calibration the PINDA temperature compensation table. To do this, we will insert G-code in our Slic3r start-up script that waits for the PINDA to cool down to (or below) 30C, and then start the heaters and wait for PINDA to heat up to 35C. In this way, the mesh bed leveling will always occur when the PINDA is at 35C. As long as we also calibrate our Live-Z value after mesh-leveling at that temperature, the Z-offset values should be consistent.

Here is some example start gcode that achieves this:

```
G28 W ; home all without mesh bed level
M104 S0 ; Turn off all heaters
M140 S0 ; Turn off all heaters
M106 S255 ; turn on fan
G0 Z100 ; PINDA cooling position
M860 S30 ; wait until PINDA is <= 30C
M107 ; turn off fan
M104 S[first_layer_temperature] ; set extruder temp
M140 S[first_layer_bed_temperature] ; set bed temp
M190 S[first_layer_bed_temperature] ; wait for bed temp
M109 S[first_layer_temperature] ; wait for extruder temp
G0 X50 Y50 Z0.15 ; this is a good PINDA heating position
M860 S35 ; wait until PINDA is >= 35C
G28 W ; home all without mesh bed level
G80 ; mesh bed leveling
```

Because the PINDA is always at 35C at the start of the print, there is no need for calibration. Of course, in theory, you could pick any other temperature; you do not “need” to be in the calibration range. But 35C is a good value that has been shown to work.

Questions?
----------

Hit me on the discord @stahlfabrik or read the super long forum thread on the Prusa forum where all that knowledge was worked on: <https://shop.prusa3d.com/forum/-f0/1st-layer-problems-in-depth-look-at-software-pinda-t14815.html> Just bear in mind, that the information on that thread is evolving: you might want to read the first post first, then continue the read from back to front - if that makes sense:-) Prusa also have a very minimal wiki page on that topic: <https://github.com/prusa3d/Prusa-Firmware/wiki/Manual-temperature-calibration>

Alternative Way to Measure Z Offsets
------------------------------------

Discord user @motocoder has come up with an alternate way to measure the per-temperature z-offsets. This alternate approach is faster because it does not require test prints. See [PINDA Temperature Calibration with Electrical Continuity](PINDA_Temperature_Calibration_with_Electrical_Continuity.md "wikilink") for details.

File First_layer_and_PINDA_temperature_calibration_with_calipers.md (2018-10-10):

In this guide we present an improved way to adjust both the frst layer height and the PINDA temperature calibration table. This method is based on the original work by _@stahlfabrik_ ([Manual_print_based_PINDA_temperature_calibration](Manual_print_based_PINDA_temperature_calibration.md)) and has the added benefit of improved precision and repeatability. Unlike the [PINDA_Temperature_Calibration_with_Electrical_Continuity](PINDA_Temperature_Calibration_with_Electrical_Continuity.md) method by _@motocoder_, no hardware of software modifications are required.

# Prerequisites

- A Prusa i3 MK3 with the original firmware version 3.3.1 or later, calibrated and capable of producing at least a remotely passable first layer;
- A digital caliper or a micrometer; and
- A specially crafted [test print ](files/First_layer_calibration_6_temp.gcode "wikilink").

You need a tool capable of measuring thickness repeatably with at least +/-0.01mm precision to have 10% error or better. A typical entry-level digital caliper should be capable of that. If you wish (and have the tool) you can use a digital or a vernier scale micrometer.

# Method

## Finding good PINDA temperature compensation values

Start with enabling _Temp. cal._ in the _Settings_ menu on the printer. Then make sure that the compensation table is zeroed out, by issuing `M861 Z` command.

```
Send: M861 Z
Recv: zerorized
Recv: ok
```

Continue with printing `First_layer_calibration_6_temp.gcode`. The print consists of 6 1-perimeter 1-layer high rectangles, each printed after performing the mesh leveling at a different PINDA temperature. As the PINDA has to cool down and reheat to exact set temperature before printing each rectangle, the print may take some time (around 30 minutes). 

This is how the print should look like once it has finished:

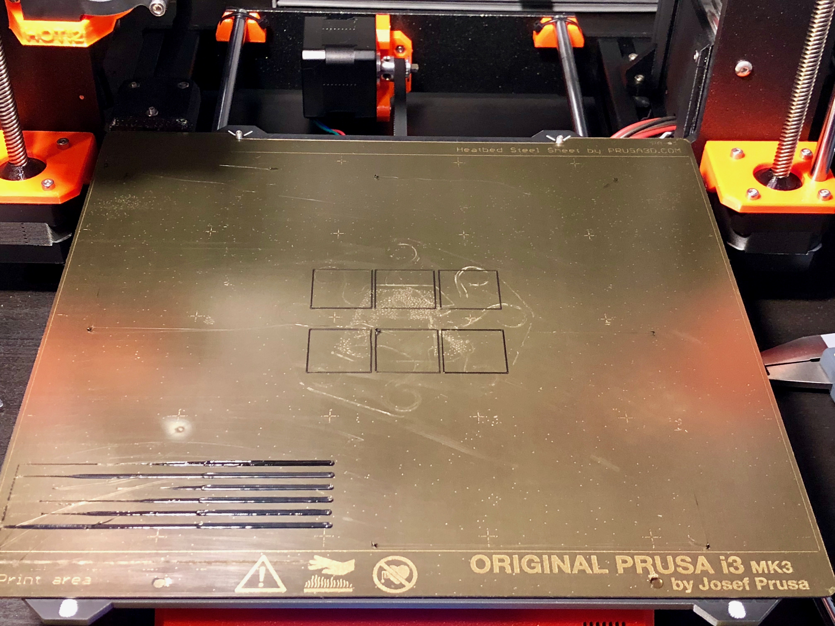
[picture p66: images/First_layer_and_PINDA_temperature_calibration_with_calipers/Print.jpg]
Print overview


After letting the build plate to cool down, proceed to carefully removing rectangles with tweezers or scraper one-by-one.

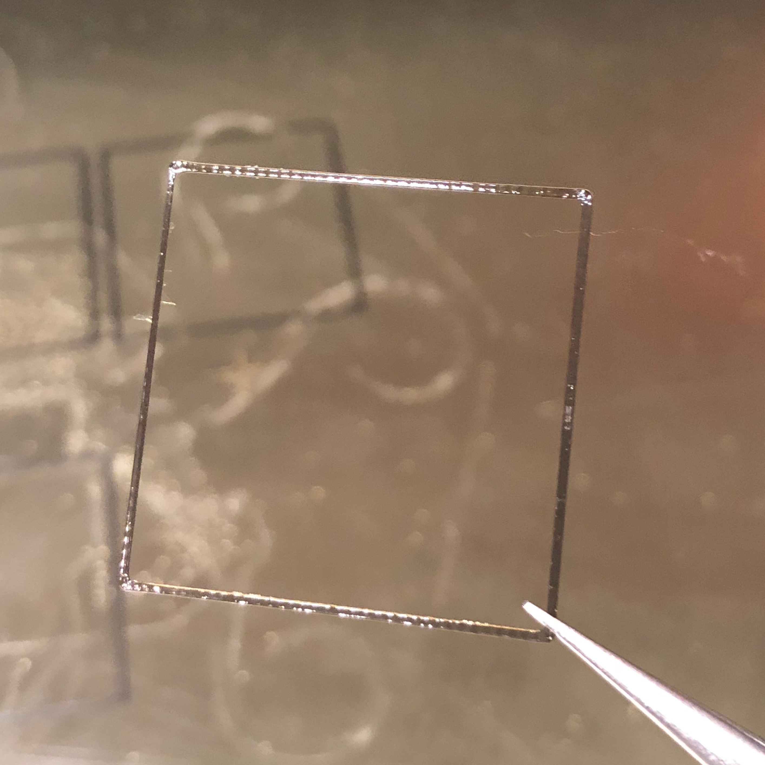
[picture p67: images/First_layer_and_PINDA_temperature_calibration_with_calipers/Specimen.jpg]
Specimen


Measure each rectangle, closing the flat part of the caliper jaws across the two sides of a corner, but leaving the very tip of the corner out, as there may be a bulge. Repeat for each corner and record the high and the low value. Ideally you should be getting identical measurements across all four corners. If the measurements vary dramatically, something is wrong with your mesurement tool, or your bed, and you need to troubleshoot.

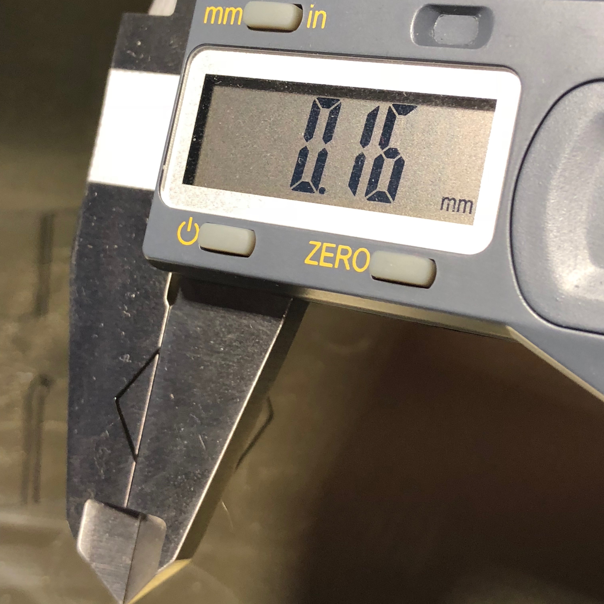
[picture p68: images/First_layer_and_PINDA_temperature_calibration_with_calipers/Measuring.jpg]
Measuring


Keep in mind which rectangle was printed at which PINDA temperature:

```
,-----, ,-----, ,-----,
| 35º | | 40º | | 45º |
`-----` `-----` `-----`
,-----, ,-----, ,-----,
| 50º | | 55º | | 60º |
`-----` `-----` `-----`
```

Enter the measured layer heights into a table, use the highest value for each rectangle:

35º | 40º | 45º | 50º | 55º | 60º
----|-----|-----|-----|-----|----
0.16| 0.14| 0.15| 0.17| 0.15|0.16

As it can be seen, all layers have different heights. As we want the first layer to always be the same height, regardless of the PINDA temperature, a temperature compensation is needed. It can be derived as follows. The calculations are quite simple and you can do them in your head. Let _H(t)_ be the height of a layer, printed at PINDA temperature _t_. Then the compensation value (in steps) for each layer _C(t)_ is _(H(t) - H(35º)) * 400_.

In other words, each 0.01mm corresponds to 4 steps. If a layer is thinner than the reference layer (35º), the compensation value has to be negative, and positive otherwise.

For the values above, the following compensation table should be used:

40º | 45º | 50º | 55º | 60º
----|-----|-----|-----|----
 -8 |  -4 |   4 |  -4 |  0

Now program the table into your printer, using the following commands:

```
M861 S-8 I0
M861 S-4 I1
M861 S4 I2
M861 S-4 I3
M861 S0 I4
```

You can skip setting 0 compensation values, in this case, `M861 S0 I4` need not be issued. Make sure to use your own offset values after `S` and not my example ones.

Verify your table by issuing `M861 ?`.

```
Send: M861 ?
Recv: PINDA cal status: 1
Recv: index, temp, ustep, um
Recv: n/a, 35, 0, 0.00
Recv: 0, 40, -8, -20.00
Recv: 1, 45, -4, -10.00
Recv: 2, 50, 4, 10.00
Recv: 3, 55, -4, -10.00
Recv: 4, 60, 0, 0.00
Recv: ok
```

Now do the test print again and measure the rectangles. All layers should measure the same or nearly the same.

35º | 40º | 45º | 50º | 55º | 60º
----|-----|-----|-----|-----|----
0.17| 0.17| 0.16| 0.16| 0.16|0.16

Please note that the 35º layer height appeared to have changed while it should not have. This seems to always happen when the PINDA temperature compensation table is changed, for reasons unknown.

The results obtained are already very good, and if a 0.01mm caliper was used, within the measurement error.

If you wish, you can make one more iteration. In this case it would make sense to add -2 steps to 45, 50, 55, and 60º compensation values. These values are more of a guess than exact science, because we are below the resolution of the measurement tool (unless using a micrometer). Please note that whatever correction values come up with during this and any further iterations, you will have to **add** to the previously set values and not replace them.

## Adjusting the first layer

Now you can adjust your first layer for perfect adhesion. There are two ways to do it:

- The traditional way is to decrease the first layer height using Live Z adjustment until the filament reliably adheres to the printing surface. For me it happens at aroung 0.16mm measured first layer height. The disadvantage is that the height of all printed objects will be lower than it should be.
- The alternative way is to set the first layer height to exactly 0.2mm and increase the first layer flow in the slicer until the filament adheres reliably. The advantages are that this can be configured per-filament and that the object height is unaffected.

Enjoy your perfect first layer!

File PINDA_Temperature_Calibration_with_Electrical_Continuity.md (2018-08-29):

On this page we describe a slight modification of the PINDA temperature compensation table calibration process described in [Manual print based PINDA temperature calibration](Manual_print_based_PINDA_temperature_calibration "wikilink"). This modified approach gives similar results, and for some better results (those who have a hard time judging the z-offset by observing the first layer quality). However, it requires some equipment that not every user will have access to, so for most users @stahlfabrik's approach is recommended.

### Summary

The alternate measurement method uses electrical continuity to detect when the nozzle is touching the heatbed. A circuit is created, using either some wire and a multimeter, or a battery, LED, and resistor. The mesh bed leveling is initiated with the PINDA at some set temperature, as described in @stahlfabrik's article. After this, however, the nozzle is moved over a small piece of conductive tape that has been placed on the steel heatbed sheet. The nozzle is lowered using the Live-Z offset feature until it just touches this tape. The nozzle touching the tape closes a circuit, allowing current to flow. The flow of current either causes a multimeter in continuity test mode to beep, or causes an LED to light up. The user then records the Live-Z offset value and repeats this process for the remaining PINDA temperature calibration values.

### Equipment Needed

For this technique you will need the following equipment:

1.  Small gauge electrical wire (TODO: Insert length)
2.  A multimeter with a continuity or ohms setting. Alternatively, you can use an LED, resistor, and battery.
3.  A small piece of [copper tape](https://www.amazon.com/gp/product/B007Y7FV2O/ref=oh_aui_search_detailpage?ie=UTF8&psc=1), or some other conductive surface, that can be attached to the steel PEI sheet.
4.  (Optional) Alligator clips or multimeter probe leads with some sort of clip on them

### Measurement Set-up

Before taking the measurements, you will need to set up a few things. First, heat up the nozzle and unload the filament. Then wait for the hotend to completely cool down before proceeding.

Next, you will need to attach a wire to the heatblock. Strip the insulation from both ends of the wire. It is recommended that you attach the wire to the hot-end by loosening slightly the screw that holds the heater in place. Loop the wire around this screw and tighten it back down. Route the wire along the extruder wire bundle. You can use a few zip ties to secure it. Let the wire hang down on the left side of the printer.

Attach one lead of your multimeter to this wire on the left hand side of your printer. I have some alligator clip leads for my multimeter, so I just used those. Alternatively, you can try and wrap the wire around the probe end, and then tape it in place. The exact method you use to affix it is not important; the goal is to not have to hold the wire in place while taking the measurement. Put your multimeter in Ohms/Continuity-Test mode (the one where it beeps when you touch the two probes together). If you do not have a multimeter, you can build a small circuit with a battery, LED, and (current-limiting) resistor.

Next we will attach the copper tape to the steel sheet. Cut a piece of this tape about 5cm in length. Fold the left-hand 1 cm back upon itself to make a section that will not stick. Stick the tape to the heatbed. I recommend placing it about one cm in front of the line that runs left to right on the heat bed, about midway front to back. The right hand side of the tape should be approximately centered left-to right, with the portion you stuck back upon itself on the left side. Flatten the right hand side of the tape as much as possible. I used a small plastic spatula/scraper for this.

Here is a picture of my printer set up for a measurement:

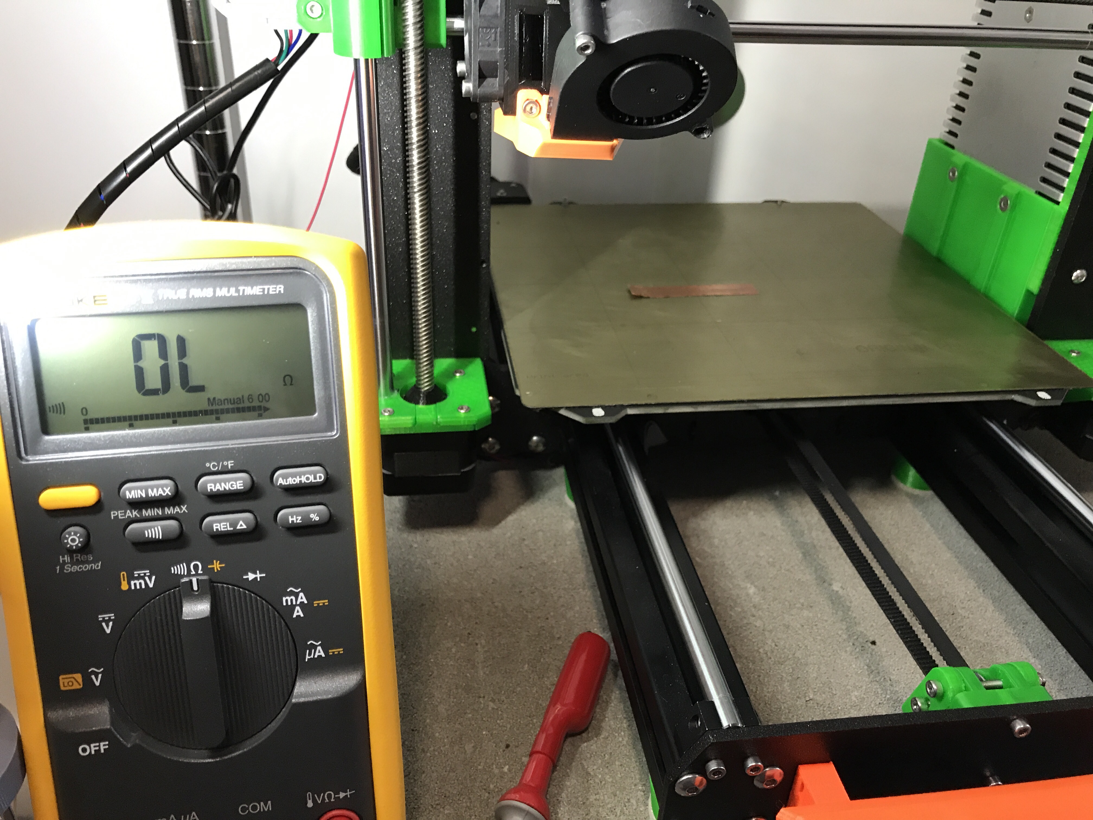
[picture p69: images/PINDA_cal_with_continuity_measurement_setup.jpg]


Now using the printer “Settings/Move Axis” menu, move the print head until the nozzle is centered over the section of tape you flattened out. Note the X and Y values, as we will need to insert these in our G-code later.

Before proceeding, please follow-the set-up instructions in [@stahlfabrik's article](Manual_print_based_PINDA_temperature_calibration "wikilink"), specifically disabling Temp Cal in the menus:

1.  In the printer menu, turn the setting for “Temp. Cal.” to “off”.
2.  Use the terminal to your printer to send the command “M861 Z”. This sets all offsets to zero. You can verify that the values were cleared to zero by sending “M861 ?”. This g-code command will instruct the printer to output the current offsets in the EEPROM table.

### Taking a Measurement

The process to prepare the printer for the measurement is very similar to that described in the aforementioned article.

1.  Run some g-code that will heat up the PINDA to a desired temperature, run a mesh bed level, and then position the nozzle over the copper tape
2.  Attach the other probe of our multimeter to that little flap of the copper tape on the left hand side. I use an alligator clip on the end of the probe for this, but use whatever technique works best for you.
3.  Carefully lower the nozzle using the Live-Z Offset feature in the printer menu until the nozzle just touches the copper tape. We will know when it touches the tape because our multimeter will beep (or our LED will light). We want to go slow when lowering the nozzle, so that we don't ram the nozzle into the bed and cause the motors to skip a step. If you do that, I recommend you note the approximate value, repeat the whole measurement at this temp (re-run the g-code), and then knowing the approximate value be more careful about lowering this time.
4.  Record the z-offset value and the associated PINDA temp. **Before you proceed to the next measurement, be sure and remove the probe clip from the tape.**

I recommend you use the bed temperatures described in [@stahlfabrik's article](Manual_print_based_PINDA_temperature_calibration "wikilink"), but for all measurements set the nozzle temperature to 170C, and leave it there for the whole measurement. The reason for this is that the hot-end and nozzle can expand and contract with temperature changes, so to get maximum accuracy we want to keep that constant throughout the test. For convenience, here is stahlfabrik's table of recommended bed temperatures:

| PINDA target temp | Used bed temp |
|---|---|
| 35C | 60C |
| 40C | 60C |
| 45C | 60C |
| 50C | 80C |
| 55C | 90C |
| 60C | 100C |

### Sample G-Code

Here is some sample g-code for a measurement at 60C

```
; cooldown
M104 S0 ; set extruder temp
M140 S0 ; set bed temp
G28 W ; home all without mesh bed level
G0 Z100 ; Cooling PINDA position
M106 S255 ; Turn fan on
M860 S58; UPDATE WITH PINDA TARGET TEMP MINUS TWO
M107 ; Turn fan off
; warmup
M104 S170 ; set extruder temp
M190 S110 ; UPDATE WITH THE APPROPRIATE BED TEMP
G0 X50 Y50 Z0.15 ; this is a good PINDA heating position
M860 S60 ; UPDATE WITH THE APPROPRIATE PINDA TEMP
; start the print
G28 W ; home all without mesh bed level
G80 ; mesh bed leveling
G0 X129 Y93 Z0.15 F1000 ; UPDATE WITH YOUR X AND Y VALUES
M300 S1396 P714 ; Beep so we know it is ready
```

This g-code will first wait for the PINDA to cool off, before heating the bed and nozzle. Once the bed has reached temperature, it will move the PINDA down close to the bed and wait for it to heat to the target temperature. Then it will perform a mesh bed level and then move the nozzle over the tape. Finally, it will tell the printer to beep so that you know it is ready for a measurement.

In the g-code above, make sure you update the following values:

-   Update the PINDA cooldown target temp on the line that says “UPDATE WITH PINDA TARGET TEMP MINUS TWO”
-   Update the target bed temperature on the line that says “UPDATE WITH THE APPROPRIATE BED TEMP”
-   Update the target PINDA temp on the line that says “UPDATE WITH THE APPROPRIATE PINDA TEMP”
-   On the second to last line, update the X and Y values here with the ones you noted when aligning the nozzle over the copper tape.

The remainder of the process is identical to that described in (you guessed it) [@stahlfabrik's article](Manual_print_based_PINDA_temperature_calibration "wikilink"). I've included those steps here so you don't have to ping-pong back and forth between the two articles.

### Calculate offsets

Now that we have the Live-Z offset values, we calculate the ustep values:

```
usteps(T) = (live_adjust(35) - live_adjust(T)) * 400
```

The ustep values have to be integers, so round them off. Be careful to keep track of the sign; the sign is important! I mostly get negative values, but others often get more positive values.

### Store offsets in EEPROM

To store the values to the EEPROM, we use that first new code again: M861

To store -5 for the 40C value, you send the printer “M861 S-5 I0”. And as another example, to store 11 in the 45C offset value, sou send “M861 S11 I1”. So, “I” denotes the index into the EEPROM table, ranging from 0 for 40C to 4 for 60C - remember the value for 35C is the reference point and thus always zero.

By the way, if you want the old standard EEPROM table, you can set that with “M861 !”. I already mentioned that “Z” zeroes the table and “?” queries and prints the table.

### Enable temperature calibration

Now that our EEPROM table is full of reasonably accurate calibration values, we should re-enable temperature compensation in the printer menu. Got to “settings” and enable “temp. cal.”.

How to take advantage of the temperature calibration table
----------------------------------------------------------

So now that you have calibrated the temperature compensation table, you need to make sure that your PINDA is always in the temperature range of 35C to 60C before the printer homes and does the mesh bed leveling. A very easy way to do that is to use the code M860 code again. Because the PINDA calibration starts at 35C, we just need to insert an M860 g-code to tell the printer to start a print only when the PINDA is at or above that value. The g-code snippet below shows how to do that, for the Slic3r slicing software (put this in your Start g-code in the printer definition). Note that the M860 occurs **after** the bed and nozzle heaters are turned on. We want this because we want the printer to check the PINDA temp is at **or above** the specified value.

```
G28 W ; home all without mesh bed level
M104 S[first_layer_temperature] ; set extruder temp
M140 S[first_layer_bed_temperature] ; set bed temp
M190 S[first_layer_bed_temperature] ; wait for bed temp
M109 S[first_layer_temperature] ; wait for extruder temp
G0 X50 Y50 Z0.15 ; this is a good PINDA heating position
M860 S35 ; wait until PINDA is >= 35C
G28 W ; home all without mesh bed level
G80 ; mesh bed leveling
```

### Calibrate Live Z at 35C

Since this process does not include calibration of the Live-Z offset, we need to do that now. Load some filament in your printer, and go through the normal calibration process. Be sure and use the G-code snippet above (or something equivalent), so that your PINDA is in the 35C - 60C range before you do this calibration.

### (Optionally) verify temperature calibration

If your Prusa i3 MK3 runs at least version 3.3.1 you can use [Temp_cal_veri_v5.gcode](files/Temp_cal_veri_v5.gcode "wikilink") gcode file. The purpose is to have a printable test to verify that the values in your EEPROM value are good. The Gcodes prints six squares in one go, on the same plate. This takes a while because the PINDA has to cool down in between printing of each square. You just have to watch and wait. The top left square is printed with a PINDA temperature of 35C, right next to it is a 40C square printed and so on. So the squares are:

```
35C 40C 45C
50C 55C 60C
```

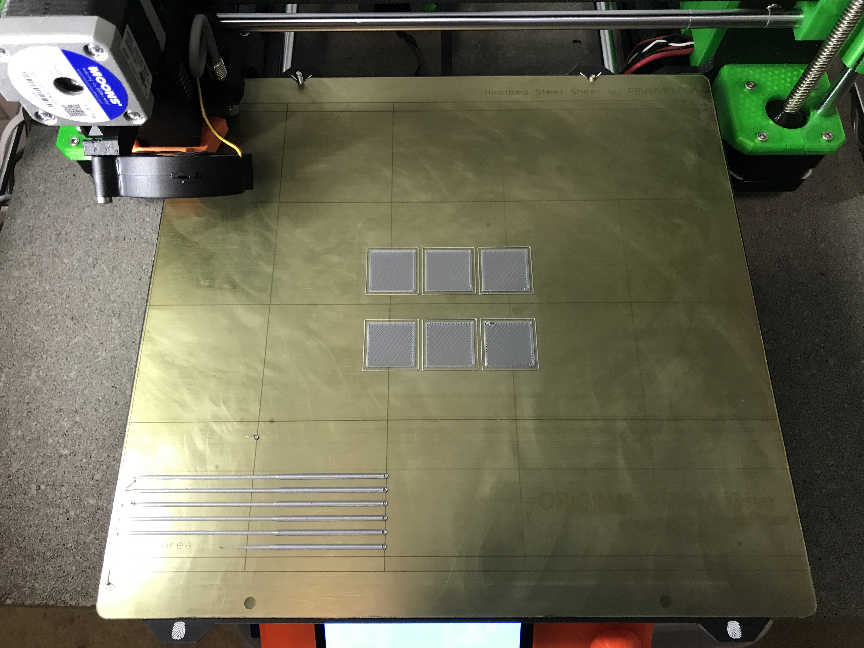
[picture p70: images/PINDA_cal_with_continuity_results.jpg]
Here is picture of what my print looks like: 

You can visually inspect the squares to make sure that each first layer looks good.

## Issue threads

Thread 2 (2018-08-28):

Skelestruder pages need reformat for Markdown

VileBrigandier, 2018-08-28:
Skelestruder's assembly pages didn't translate well into Markdown. I have fixed all the images and links jltx had originally, but they are sized oddly compared to his original work. Would be good to get jltx to go over this.

VileBrigandier, 2018-08-28:
Going to try to get this handled tonight after work. Thanks for the heads up, I will skim over the other pages with similar tables as well.

Closed 2018-08-29.

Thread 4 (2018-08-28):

Please delete the content for which I am the sole contributor

matthew-humphrey, 2018-08-28:
Please delete the following content, for which I am the sole contributor:

Bed_Leveling_with_Wave_Springs.md
Cold_Pull_on_MK3.md
Moons_stepper_motors.md
PINDA_Temperature_Calibration_with_Electrical_Continuity.md
images/Accessing_the_filament.png
images/Cleaning_Filament.JPG
images/Filament_Sensor_Light_Block.png
images/HoldingSleeveSpringAndSpacer.JPG
images/Idler_Cover_Screws.jpg
images/MoonsWiring.png
images/Moons_Extruder.JPG
images/Octoprint-MeshMap-Screenshot.PNG
images/PINDA_cal_with_continuity_measurement_setup.jpg
images/PINDA_cal_with_continuity_results.jpg
images/Skelestruder_Legend.jpg
images/Skelestruder_Legend_Alt_View.jpg
images/Sleeve.JPG
images/SleeveRetainingSpring.JPG
images/SpringInstalled.JPG

VileBrigandier, 2018-08-28:
Done.

VileBrigandier, 2018-08-28:
Contributions cleared from git history as well.

Closed 2018-08-28.

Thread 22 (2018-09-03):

Suggestion for wave spring installation page

jcwren, 2018-09-03:
First, it looks like two of the pictures are inverted (washer with straw on table, pliers holding straw). No big deal, the idea is still conveyed.

I haven't yet installed my wave-spring washers, but instead of the straw and pliers dance, what about using toothpicks? Put the toothpick in the screw hole, drop the spacer and washer on to it, then lower the print bed onto the toothpicks, one by one replace each toothpick with a screw.

It might be necessary to put a piece of tape on the bottom of the hole, and possibly clip the toothpick to a shorter length to make aligning the bed on top of them easier.

I plan to give this a shot when the wave-spring washers I ordered are delivered.

VileBrigandier, 2018-09-03:
Hi jcwren,

1. The flipped images are due to the image submitter's device using EXIF data to determine image rotation, and that breaks on some browsers. Re-opened issue #1 regarding this. The issue was closed due to the images being removed for other reasons, but now that they are back the issue is valid again.
2. The improvements you are proposing may be valid improvements for the method; however, there's also a method for doing this in a much more rigid way: https://github.com/PrusaOwners/prusaowners/wiki/Bed_Leveling_without_Wave_Springs - There may be pros/cons for each, I haven't verified the new method myself, just wanted to point this out before you tear into this using the previous method.

sarf2k4, 2018-09-08:
@VileBrigandier, I few questions regarding bed leveling without wave springs (sorry for being off topic).

I read the guide thoroughly, during the print temperature calibration, in the guide stated for example 60'c is my usual print temperature and I would have to level the bed manually with 60'c.

1. What's not mentioned is that how was the bed elevation results if the bed temperature differs from 60'c for example 80 or 100'c?
2. What about the temperature calibration, should it be turned off?
3. Do I have to run temperature calibration after doing the locknut bed leveling method?

I am planning to print several types of materials, primarily abs and pla, so this is a concern to me actually.

Thank you in advance

VileBrigandier, 2018-09-08:
@sarf2k4,

Leefla in the Prusa Discord is the author of that article and should be able to answer that. I have sold my MK3 and moved the wiki content here from a MediaWiki installation, and unfortunately it set my name on a lot of the articles. Hopefully that will fix itself with time.

Thanks!

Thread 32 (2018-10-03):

Parts list for Skelestruder missing parts

Nath5, 2018-10-03:
I have been printing the parts for the skelestruder and have noticed there are several parts missing from the parts list.  So far I have found the following to be missing:

Tensioner
Cam

I will edit if I find more.

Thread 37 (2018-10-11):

higher voltage fan info

trevjonez, 2018-10-11:
going through the [make prints better](https://github.com/PrusaOwners/prusaowners/blob/master/How_to_make_prints_better_on_the_mk3.md) page I found this:
`You will likely fail self test until a method is found to monitor RPM with these higher voltage fans.`

any more info on the why of this? Is the signal from the tach too high of a voltage?

trevjonez, 2018-10-11:
my thoughts are the existing rpm tracking is defective already. based on some quick testing I did. shown in this PR: https://github.com/prusa3d/Prusa-Firmware/pull/1193#issuecomment-428044286

trevjonez, 2018-10-11:
Is it possible to do this mod and have different voltages per fan?
https://github.com/PrusaOwners/prusaowners/blob/master/Einsy_fan_voltage_mod.md

IE: I have a 24 blower on its way and want to keep the 5v noctua until I decide on what to replace it with, without going deaf.  Can I use a buck converter since the hotend fan is typically 100% anyway?

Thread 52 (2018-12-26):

PLA Bearings seized after unenclosed ABS printing

tg73, 2018-12-26:
https://github.com/PrusaOwners/prusaowners/wiki/PLA_bearings

I've had custom PLA bearings working well for some months. I usually print PETG or PLA. After printing some ABS for the first time, bed temp 110, no enclosure, ~2h30 print time - my Y axis has nearly seized. Y axis homing thinks the end stop is wherever the bed currently is. My PLA bearings are set in 15mm stainless tube, 1.5mm wall thickness. I suspect the seizing is a side effect of the heat transfer from the bed to the housings. Maybe add a note to the wiki about this issue.

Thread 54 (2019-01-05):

Skelestruder patch for indirect filament sensor appears incomplete

tg73, 2019-01-05:
@jltx1 From what I can tell, there are two functions that need patching: `pat9125_update()` and `pat9125_update_y()`. There is also `pat9125_update_y2()`, but this does not appear to be used anywhere. All three functions contain the expression `pat9125_y -= iDY`. The [patch ](https://github.com/PrusaOwners/prusaowners/blob/master/Skelestruder_Assembly.md#editing-needed-below) only changes `pat9125_update_y()`. Is this correct?

jltx1, 2019-01-05:
When I made that patch, the only function being used for filament sensing was the one, but they may have expanded it in recent fw updates.  I currently flip all three just in case.

AbeFM, 2019-01-09:
I found two to change, and I think I ended up changing just one. and it's
working ok with ZB firmware.

line 19 pat9125.c
      pat9125_y -= iDY; //negative number, because direction switching does
not work//Abe Skelestruder Original
//      pat9125_y += iDY; //negative number, because direction switching
does not work//Abe Skelestruder Added

I didn't make the change, works fine not done.

Line 216
//Abe Skelestruder      pat9125_y -= iDY; //negative number, because
direction switching does not work
      pat9125_y += iDY; //negative number, because direction switching does
not work //Abe Skelestruder

I flipped this one.

Line 324:
     pat9125_y -= dy; //negative number, because direction switching does
not work
//      pat9125_y += dy; //negative number, because direction switching
does not work //Abe Skelestruder
Looks like I kept that one stock as well.

From what I'm running right now, it seems you only need to change the one
line ~216.

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

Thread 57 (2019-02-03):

Where is the prusa config file?

JBTERRA, 2019-02-03:
The guide speak about a mk3 config file but I can't find one to download. I have a MK2s but I hope to get this file at a starting point to configure klipper

Arksine, 2019-02-03:
It is in the PrusaOwners repo.  I have plans to merge it upstream, there are other things that need to be handled first.

https://raw.githubusercontent.com/PrusaOwners/klipper/master/config/printer-prusa-i3-mk3-2017.cfg

JBTERRA, 2019-02-04:
Thank you. Btw I've got a prusa MK2 and I've tried to adapt the config with the generic mini rambo example. It kinda work but  can't see the speed processing I thought, it seems like before with a gcode I'm using for testing.

I'm using the mk2 also as a laser engraver. With original prusa firmware (marlin) I can scan grayscale images buy it seems I hit the limit of minirambo processing capacity for gcode so I've got a cap in speed.

Thought that going to klipper could give me more speed in scanning but it seems the same.

Maybe I've one something wrong or Is normal that I can't fast scan even with klipper? (maybe is more oriented to speed up prints but gcode processing speed is the same)

Hope you can give me some hints, thanks

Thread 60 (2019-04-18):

Einsy + Banan Pi Zero + Klipper + DWC2

rafaljot, 2019-04-18:
I'm very disappointed with Rassberry Pi Zero and OctoPrint. So I made mix of
- Banan Pi Zero ,  the same size and compatible with rPi Zero, Allwiner H2+ with 4 cores, external antenna http://www.banana-pi.org/bpi-zero.html
- Ubuntu Base Minimal by @avafinger https://github.com/avafinger/bananapi-zero-ubuntu-base-minimal
- Klipper,
- DWC2 for Klipper https://github.com/Stephan3/dwc2-for-klipper

It works for now, Requires minor corrections. Boot takes ~15s. I think I can tune it and cut ~3s.
I think it is good idea to make full SD image with this setup.

What do you think about this setup ?

brunnels, 2020-01-08:
I'm running a similar setup to you and have some questions:

1.  what 0.9 degree steppers are you using and what TMC2130 settings are you using?  I think I got too high amperage steppers so I had to add heatsinks to the bottom of the einsy and a fan otherwise the extruder would skip and jam or I would get layer shifting.

2.  what do the DLP printed pulleys buy you over standard aluminum pulleys?

rafaljot, 2020-01-12:
@brunnels
1. I have 1.7amp 09 motors + fan + heatsinks on both sides.
2. I use resin pulleys just for fun :)

tillin9, 2021-02-11:
Pleasantly surprised to see this - I run a very similar setup with the exception I haven't made the jump to Klipper - though thinking about it, Did you get any improvement in print quality or speed?

I'm still not 100% satisfied with my Prusa's quality - I occasionally have VFAs depending on settings/ part geometry. Faster is always better. Was looking at replacing the Einsy with an SKR or going to Klipper to see if that helped.

Is the print quality better for you?

P.S. I love the Banana Pi Zero. Designed this - https://www.prusaprinters.org/prints/32433-einsy-enclosure-for-bpi-banana-pi-m2-zero-plus (my printer hadn't been upgraded to a bear at that time)

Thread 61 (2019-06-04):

Power Cable Update (PSU to Einsy)

Gefionious, 2019-06-04:
The parts for the power cables are incorrect for the mk3 PSU to Einsy. I was able to get the drawings from Prusa. They definitely have different spade connector sizes at either end, where your docs are incorrect. Also, there are some great PSU mounting designs on thingiverse for the Meanwell 320W PSU, which I love and which I need slightly longer cables for.
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

elektronchika, 2019-07-03:
Is this the drawing for the 240W or 320W power supply? If this is for the 240W, how long shall the cables be for the 320W one?

How long are the cables for the heated bed?

Thanks!!!

Gefionious, 2019-07-03:
This drawing is from Prusa for the standard i3 mk3/s 240W PSU with the recommended cable management. You would need it to be approximately 1"/25mm longer for the Meanwell 320W PSU using this mount from thingiverse [https://www.thingiverse.com/thing:3082178]. I have done no work on the heated bed, but they would be independent and required no changes on my end with the new PSU (i.e. the heated bed is not directly attached to the PSU, it is from the Einsy board)

Gefionious, 2019-07-05:
This drawing is for the 240W standard PSU, they would need to be about an inch or 25mm longer for the meanwell 320W PSU mounted with one of the thingiverse mounts: https://www.thingiverse.com/thing:3082178

mkolassa, 2022-08-08:
For those who come after...

So far I've tracked down two sets of flanged fork connectors which may be the correct items.

The first comes from a-dude16 on the Prusa forums at...

https://forum.prusa3d.com/forum/original-prusa-i3-mk3s-mk3-user-mods-octoprint-enclosures-nozzles/extending-the-psu-cables./paged/3/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

The other ones are from Morris Products:

PSU Side: Morris Products 11810 Nylon Insulated Flange Fork/Spade Terminals - 16-14 Wire, # 6 Stud
Einsy Side: Morris Products 11802 Nylon Insulated Flange Fork/Spade Terminals - 22-16 Wire, # 4 Stud

mkolassa, 2022-08-08:
Looks like there's a discrepancy in the spec sheets provided by Morris Products.  It may actually be the 11812 and 11804.

I'm ordering both sets and will confirm the correct one once I get them.

mkolassa, 2022-08-26:
Sadly, my orders had to be cancelled as the vendor was actually out of stock.

It's incredibly difficult to find a vendor that doesn't require purchase of a bag of 100x of these things, at least in the USA.

jhoblitt, 2022-08-26:
Terminals can now be purchased directly from te.com in "sample" quantities (single units). Tyco is superior molex iny experience.

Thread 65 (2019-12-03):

Klipper on MK3S

brotherdust, 2019-12-03:
I followed the guide to getting Klipper set up on MK3S, but ran into an issue on the firmware flash step. The printer gets stuck on "updating... do not disconnect". The flash utility indicates that the flash was successful.

Rebooted the printer and it's just stuck at the boot screen now (Prusa i3...). Any thoughts?

Arksine, 2019-12-03:
Most likely its an issue with the configuration, there have been some config breaking changes recently and I haven't had a chance to update the sample configuration.  If you check /tmp/klippy.log it will tell you what is wrong.

brotherdust, 2019-12-03:
Here's the result of the flashing process:
```
pi@octopi:~/klipper $ make flash FLASH_DEVICE=/dev/serial/by-id/usb-Prusa_Research__prusa3d.com__Original_Prusa_i3_MK3_CZPX1519X004XK20483-if00
  Flashing out/klipper.elf.hex to /dev/serial/by-id/usb-Prusa_Research__prusa3d.com__Original_Prusa_i3_MK3_CZPX1519X004XK20483-if00 via avrdude

avrdude: AVR device initialized and ready to accept instructions

Reading | ################################################## | 100% 0.01s

avrdude: Device signature = 0x1e9801 (probably m2560)
avrdude: reading input file "out/klipper.elf.hex"
avrdude: writing flash (23720 bytes):

Writing | ################################################## | 100% 4.19s

avrdude: 23720 bytes of flash written
avrdude: verifying flash memory against out/klipper.elf.hex:
avrdude: load data flash data from input file out/klipper.elf.hex:
avrdude: input file out/klipper.elf.hex contains 23720 bytes
avrdude: reading on-chip flash data:

Reading | ################################################## | 100% 3.05s

avrdude: verifying ...
avrdude: 23720 bytes of flash verified

avrdude: safemode: Fuses OK (E:FD, H:D0, L:FF)

avrdude done.  Thank you.
```

Here's the output from `/tmp/klippy.log`:
```
cat /tmp/klippy.log
Starting Klippy...
Args: ['/home/pi/klipper/klippy/klippy.py', '/home/pi/printer.cfg', '-l', '/tmp/klippy.log']
Git version: 'v0.6.0-1892-g5aa5b0f4'
CPU: 4 core ARMv7 Processor rev 4 (v7l)
Python: '2.7.13 (default, Sep 26 2018, 18:42:22) \n[GCC 6.3.0 20170516]'
Start printer at Tue Dec  3 12:36:45 2019 (1575401805.1 9.4)
===== Config file =====
[probe]
pin = PB4
x_offset = 24
y_offset = 5
z_offset = 0
speed = 10.0

[bed_mesh]
speed = 100
min_point = 11,1
max_point = 215,193
probe_count = 3,3
mesh_pps = 2,2
algorithm = lagrange

[homing_override]
gcode =
        G1 Z3
        G28 X0 Y0
        G1 X101 Y100 F5000
        G28 Z0
axes = Z
set_position_x = 0
set_position_y = 0
set_position_z = 0

[gcode_macro G80]
gcode =
        G28
        BED_MESH_CALIBRATE
        G1 X0 Y0 Z0.4 F4000

[gcode_macro G81]
gcode =
        BED_MESH_OUTPUT

[stepper_x]
step_pin = PC0
dir_pin = !PL0
enable_pin = !PA7
step_distance = .01
endstop_pin = tmc2130_stepper_x:virtual_endstop
position_endstop = 0
position_max = 250
homing_speed = 50
homing_retract_dist = 0

[tmc2130 stepper_x]
cs_pin = PG0
microsteps = 16
interpolate = True
run_current = .281738
hold_current = .281738
homing_current = .149155
sense_resistor = 0.220
diag1_pin = !PK2
driver_iholddelay = 8
driver_tpowerdown = 0
driver_tbl = 2
driver_toff = 3
driver_hend = 1
driver_hstrt = 5
driver_pwm_freq = 2
driver_pwm_grad = 2
driver_pwm_ampl = 230
driver_pwm_autoscale = True
driver_sgt = 3

[stepper_y]
step_pin = PC1
dir_pin = PL1
enable_pin = !PA6
step_distance = .01
endstop_pin = tmc2130_stepper_y:virtual_endstop
position_endstop = -4
position_max = 210
position_min = -4
homing_speed = 50
homing_retract_dist = 0

[tmc2130 stepper_y]
cs_pin = PG2
microsteps = 16
interpolate = True
run_current = .3480291
hold_current = .3480291
homing_current = .182301
sense_resistor = 0.220
diag1_pin = !PK7
driver_iholddelay = 8
driver_tpowerdown = 0
driver_tbl = 2
driver_toff = 3
driver_hend = 1
driver_hstrt = 5
driver_pwm_freq = 2
driver_pwm_grad = 2
driver_pwm_ampl = 235
driver_pwm_autoscale = True
driver_sgt = 3

[stepper_z]
step_pin = PC2
dir_pin = !PL2
enable_pin = !PA5
step_distance = .0025
endstop_pin = probe:z_virtual_endstop
position_max = 200
position_min = -2
homing_speed = 13.333

[tmc2130 stepper_z]
cs_pin = PK5
microsteps = 16
interpolate = True
run_current = .53033
hold_current = .53033
homing_current = .348029
sense_resistor = 0.220
diag1_pin = !PK6
driver_iholddelay = 8
driver_tpowerdown = 0
driver_tbl = 2
driver_toff = 3
driver_hend = 1
driver_hstrt = 5
driver_pwm_freq = 2
driver_pwm_grad = 4
driver_pwm_ampl = 200
driver_pwm_autoscale = True
driver_sgt = 4

[extruder]
step_pin = PC3
dir_pin = PL6
enable_pin = !PA4
step_distance = .0035714
nozzle_diameter = 0.400
filament_diameter = 1.750
max_extrude_cross_section = 50.0
max_extrude_only_distance = 500.0
max_extrude_only_velocity = 120.0
max_extrude_only_accel = 1250.0
heater_pin = PE5
sensor_type = ATC Semitec 104GT-2
sensor_pin = PF0
control = pid
pid_kp = 16.13
pid_ki = 1.1625
pid_kd = 56.23
min_temp = 0
max_temp = 305

[tmc2130 extruder]
cs_pin = PK4
microsteps = 32
interpolate = True
run_current = .513757
hold_current = .513757
homing_current = .314883
sense_resistor = 0.220
diag1_pin = !PK3
driver_iholddelay = 8
driver_tpowerdown = 0
driver_tbl = 2
driver_toff = 3
driver_hend = 1
driver_hstrt = 5
driver_pwm_freq = 2
driver_pwm_grad = 4
driver_pwm_ampl = 240
driver_pwm_autoscale = True
driver_sgt = 3

[heater_bed]
heater_pin = PG5
sensor_type = EPCOS 100K B57560G104F
sensor_pin = PF2
control = pid
pid_kp = 126.13
pid_ki = 4.3
pid_kd = 924.76
min_temp = 0
max_temp = 125

[heater_fan nozzle_cooling_fan]
pin = PH5
heater = extruder
heater_temp = 50.0
fan_speed = 1.0

[fan]
pin = PH3

[mcu]
serial = /dev/serial/by-id/usb-Prusa_Research__prusa3d.com__Original_Prusa_i3_MK3_CZPX1519X004XK20483-if00

[display]
lcd_type = hd44780
rs_pin = PD5
e_pin = PF7
d4_pin = PF5
d5_pin = PG4
d6_pin = PH7
d7_pin = PG3
encoder_pins = ^PJ1,^PJ2
click_pin = ^!PH6

[printer]
kinematics = cartesian
max_velocity = 300
max_accel = 1500
max_z_velocity = 10
max_z_accel = 200

[static_digital_output debug_led]
pins = !PB7

[output_pin BEEPER_pin]
pin = PH2
pwm = True
value = 0
shutdown_value = 0
cycle_time = 0.001
scale = 1000

[gcode_macro M300]
default_parameter_s = 1000
default_parameter_p = 100
gcode =
        SET_PIN PIN=BEEPER_pin VALUE={S}
        G4 P{P}
        SET_PIN PIN=BEEPER_pin VALUE=0

[menu __filament __load]
type = command
name = Load Filament
gcode =
        LOAD_FILAMENT

[menu __filament __unload]
type = command
name = Unload Filament
gcode =
        UNLOAD_FILAMENT

[menu __filament __feed]
type = input
name = Feed Filament: {0:.1f}
parameter = 0
input_step = 1
gcode =
        M83
        G1 E{0:.1f} F400

[prusa_gcodes]
=======================
bed_mesh: generated points
0: (11.0, 1.0)
1: (113.0, 1.0)
2: (215.0, 1.0)
3: (215.0, 97.0)
4: (113.0, 97.0)
5: (11.0, 97.0)
6: (11.0, 193.0)
7: (113.0, 193.0)
8: (215.0, 193.0)
Declaration of '__filament __load' hides previous menuitem declaration
Declaration of '__filament __unload' hides previous menuitem declaration
Declaration of '__filament __feed' hides previous menuitem declaration
Extruder max_extrude_ratio=20.787584
Config error
Traceback (most recent call last):
  File "/home/pi/klipper/klippy/klippy.py", line 138, in _connect
    self._read_config()
  File "/home/pi/klipper/klippy/klippy.py", line 135, in _read_config
    pconfig.check_unused_options(config)
  File "/home/pi/klipper/klippy/configfile.py", line 260, in check_unused_options
    section,))
Error: Section 'prusa_gcodes' is not a valid config section
```

Here's the result on the printer screen:
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

Hopefully that helps?

brotherdust, 2019-12-03:
Update: taking the `[prusa_gcodes]` section out of the printer.cfg fixed it. =)

Closed 2019-12-03.

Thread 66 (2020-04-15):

bed skew correction

brunnels, 2020-04-15:
Is it possible to take the bed skew correction calculations that the prusa firware makes during "XYZ Calibration" and convert them into skew correction settings for klipper?

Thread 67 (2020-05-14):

Great Plugin .. Thanks, I habe a question for style sheets

AndreasBrauckmann, 2020-05-14:
When i work with themeify and change .container width from the web ui to this values the order and alignment from bedvalue bedvalue-0 to 8 is confused.

Is it possible to correct it with a specified style sheet?

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

Great Plugin, thanks a lot

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

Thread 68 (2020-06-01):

Klipper on MK3S

rkolbi, 2020-06-01:
I cannot get the MK3S to successfully load the Klipper.elf.hax firmware. I have built it / followed the instructions here as well as the Klipper site, the firmware seems to be properly built by the RPI, I disconnect the RPI from AMA0, at USB cable, and flash the firmware but it just hangs. On hard reboot (off/on) the LCD screen just stays frozen on the initial Prusa screen.
I have tried making the firmware on Ubuntu and then flashing it over but the same thing happens. I also tried to use prusaslicer to send the firmware to the printer with the same result, but oddly enough verification goes to 101%. In all these instances and attempts, no error messages are displayed.
The printer is resolved by reflashing the marlin firmware via prusaslicer.

It would seem as if the printer control board is locked somehow to not allow such firmware. It seems odd because I am using a self-modified version of 3.9.0 and that is no problem at all.

Any help or insight would be greatly appreciated.

Closed 2020-11-17.

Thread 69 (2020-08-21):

Opposite Connectors

mneumark, 2020-08-21:
Regarding this page:
https://github.com/PrusaOwners/prusaowners/wiki/MK3_Compatible_Parts

It would be super useful to know the opposite connectors. For example, the 50-57-9402 (power panic cable), it would help to know the connector that this snaps in to.

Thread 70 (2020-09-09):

Bed Wont level Fully

GhostHackNinja, 2020-09-09:
Printer: MK3S with BondTech upgrade
https://www.bondtech.se/en/product/prusa-i3-mk3s-extruder-upgrade/

Issue: after installing the Nylock Nuts. i but bubble levels all around, it looked pretty good. but now my printer wont Calibrate at all. could it be due to the height? what have i done wrong? i have the center piece the same as the original as requested.

p3ck, 2020-09-09:
I believe I had to do a full reset or full calibration.  Can't remember exactly what it was called..

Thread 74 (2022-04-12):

Stop waiting for calibration to complete

turboc1208, 2022-04-12:
I just installed the nyloc bed mod.  When I started the bed leveling in the prusa  bed leveling addon, it had an error almost immediately.  I needed to adjust one of the screws quite a bit.  But the prusa keeps tryiing to calibrate.  Can we have a stop or abort button or even better, recognize the error prusa sends back and stop the calibration loop.

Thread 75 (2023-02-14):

MK52 Bed connector

igaralf, 2023-02-14:
Does anyone know tha part number or vendor for the ring connector that attached to the MK52 heatbed?

Lichtjaeger, 2023-02-14:
Are you asking for ordinary [ring terminals](https://www.mcmaster.com/ring-lugs/insulated-ring-terminals/)?

igaralf, 2023-02-14:
i'm asking about these(they are listed on ebay). they seem to be non-standard, with a beefier tongue

Sent from Outlook for iOS<https://aka.ms/o0ukef>
________________________________
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

Lichtjaeger, 2023-02-14:
Oh, they are standard and pretty common too. (At least here in Europe.) They are metric.
3.2mm hole for M3 screws. The red insulation shows it's for 1 to 1.5mm² wires.

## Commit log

2018-08-28 HW table updated
    Term "screw" added where needed
2018-08-28 Adding my profiles
    0.6mm Production profiles
    Useful for very strong parts in either PETG or PC.
2018-08-28 Added Profiles and linked
    Added my configs for production parts and linked them in the slicer profiles page (there were previously no 0.6mm profiles)
2018-08-29 Fixed Skelestruder BOM table
2018-08-29 Huge amount of fixes from MediaWiki conversion
    [1st_layer_35C.stl]
2018-08-29 Revert "Fixing a ton of stuff"
    [1st_layer_35C.stl]
2018-08-29 Bringing changes back in
    This reverts commit b61f865a51b017c7b7f717eb5e705eeb83857fd4.
    [1st_layer_35C.stl]
2018-08-30 Purchase links updated for UK sources
    * Fixed assembly link
    * Purchase information on motor and motor cable plug updated for UK supplies
    * UK motor purchase information updated
    * PTFE tube purchase source updated (UK)
    * PTFE purchase location updated
    * Changed back
2018-09-08 Update Skelestruder_Assembly.md (#23)
    update patch, add MMU nut link
2018-09-17 Added Slicer Profiles for RealFilament brand - PETG (#24)
    * Added REAL Filament Configs
2018-09-17 Prusa Klipper install additional detail
2018-09-17 Create MK2 PINDA temperature compensation retrofit.md
2018-09-18 Update MK2 PINDA temperature compensation retrofit.md
2018-10-06 Add motor cable length table to Moons stepper motor page
2018-10-07 Update Einsy voltage mod
    Adds compatibility to higher-RPM fans.
    Improve ATMEGA2560 robustness.
    Easier wiring to the input voltage on the bottom side.
2018-10-10 New PINDA temperature calibration guide (#36)
    * Draft version of the guide
    * Fix typos, add links to other guides
    * Add a section on the first layer height adjustment
    * Expand the paragraph explaining the second iteration
    * Add a link to the PINDA calibration guide to the TOC.
    * Update the list of MK3 compatible parts
    - Added 2-pin Molex connector to the list,
    - Added TME links for us, humble Europeans,
    - Fixed typos,
    - Added references to original HellermannTyton textile wrap sleeves.
    * Attempt to prevent unwanted wrapping in table columns
    - Because Markdown tables are pain.
    * Fix a typo introduced in the previous edit
2018-10-18 klipper: Update documentation to represent most recent version of Klipper.
2018-10-28 Add attribution and a link to Chris Warkocki's blog to the Moons stepper motors page
2018-10-28 Add More communities and mods
    Adding Haribo Mod (the bear mod's namesake) and a link to the 3d Printing Mattermost Server.
2018-11-10 Update Skelestruder_Assembly.md
    Corrected some errors in the plastic selection table, added PETG-CF and Nylon-CF.
    - Changed glass transition temperature to heat deflection temperature.
    Glass transition temperature is not useful. It only has a very formal, material science definition that has nothing to do with actual mechanical properties. Heat deflection temperature however is very useful - it's the temperature a fixed amount of force (268 psi) will result in the same amount of bending/sagging/deflection. This is what actually matters and what I believe jltx intended to convey with this table.
    As for why glass transition temperature is not useful... take Nylon and PETG for example.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
2018-11-18 Print-based PA calibration guide
2018-11-20 Klipper.md: Fix some deprecated gcodes, and few fixes to Pressure Advance instructions
2018-12-12 Add mk3 compatible parts (#49)
    * clean up and add PSU section
    * fix PSU references
    * add Power Cables and Connectors section
    * fix PSU references
    * add Power Cables and Connectors section
    * add detailed specs for LDO motors
2018-12-12 Markdown lint and updates to the Bed Leveling info
2019-03-16 Add filament sensor configuration examples for Klipper
    Added a section on configuring the filament run-out sensors for the MK3 and MK3S.
